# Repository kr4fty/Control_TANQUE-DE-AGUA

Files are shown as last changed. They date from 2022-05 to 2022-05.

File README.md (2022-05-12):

# Control de carga para TANQUE DE AGUA
 La función del circuito es la de encender/apagar un motor el cual llena un<br>
 tanque de agua. Sería reemplazo directo a los conocidos flotadores mecánicos.
<br>

<br>
## Objetivo
 El objetivo es la realización de un circuito que controle al motor, logrando<br>
 el llenado del tanque con la menor cantidad de encendidas. De esta forma se<br>
 intenta ahorrar energía, ya que al encender el motor este consume unas 6 veces<br>
 la corriente nominal de trabajo.<br>
 También se intentara diseñar el circuito con la menor cantidad de componentes y<br>
 de esta forma lograr que sea mas económico en comparación a los flotadores.<br>
 Y por ultimo, el objetivo final seria lograr ser el reemplazo directo, UNO a<br>
 UNO entre los dos dispositivos (electrónico - mecánico), no agregando mas<br>
 cables ni fuentes adicionales a los ya existentes.<br>

## Ventajas
 * Mas económico en comparación al flotador mecánico
 * Menor consumo de energía, ya que solo se activara cuando llegue al nivel<br>
   seteado
 * ...

## Desventajas
 * Fuente de continua, se debería agregar esta fuente para alimentar el control
 * Dependiendo los sensores utilizados, se debería hasta agujerear al taque

## Futuras Modificaciones por mi (Kr4fty)
 * ~~Utilizar una fuente capacitiva que me convierta los 220Vac a los 12Vdc~~
 * ~~Modificar/corregir el circuito, ya que por ejemplo si seteamos que el nivel<br>
   mínimo de agua a un 25% y este sensor falla, es decir queda ABIERTO, el<br>
   motor seguiría funcionando indefinidamente. Lo mismo sucede con el sensor de<br>
   75%~~
 * Optimizar el circuito para tratar de utilizar la menor cantidad de componen_<br>
   tes electrónicos

## Autor original
 [ELECTROALL](https://github.com/ELECTROALL)

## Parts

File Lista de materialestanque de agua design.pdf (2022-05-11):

TANQUE-DE-AGUA

Página 1

Component Count: | 48
Ref | Qnty | Value | Cmp name
BTN1, | | 1 Encendido | SW_DIP_x01
C1, C3, | | 2 470uF | C_Polarized
C2, C4, | | 2 100nF | C
C31, | | 1 1000nF | C
C32, | | 1 100uF | C_Polarized
D1, | | 1 D_Bridge_+-AA | D_Bridge_+-AA
D2, | | 1 20% | LED_Filled
D3, | | 1 40% | LED_Filled
D4, | | 1 60% | LED_Filled
D5, | | 1 80% | LED_Filled
D6, | | 1 100% | LED_Filled
D7, | | 1 ENCENDIDO | LED_Filled
H1, H2, H3, H4, | | 4 MountingHole | MountingHole
J1, | | 1 Vca_IN | Conn_01x02
J2, | | 1 Vca_OUT | Conn_01x02
J5, | | 1 HX30002-BA | Conn_02x03_Odd_Even
Q1, | | 1 2N3904 | 2N3904
R2, R10, R11, R12, R13, R14, | | 6 1K | R_US
R3, | | 1 10K | R_US
R15, R16, R17, R18, R19, | | 5 330R | R_US
R20, R21, | | 2 330R | R_US
R22, | | 1 470R | R_US
R31, | | 1 50R | R_US
R32, | | 1 1M | R_US
SW1, | | 1 Nivel MAX | SW_Push_SPDT
SW2, | | 1 Nivel Min | SW_Push_SPDT
T1, | 1 Transformer_1P_1S Transformer_1P_1S
U1, | | 1 74HC00 | 74HC00
U2, | | 1 ULN2003 | ULN2003
U3, | | 1 LM7805 | LM7805_TO220
U4, | | 1 74HC14 | 74HC14
U5, | | 1 MOC3021M | MOC3021M
U6, | | 1 BTA16-600C | BTA16-600C

TANQUE-DE-AGUA

Página 2

## Footprint

Button_Switch_THT:SW_PUSH_6mm_H4.3mm

Capacitor_THT:CP_Radial_D8.0mm_P3.50mm

Capacitor_THT:C_Disc_D7.5mm_W2.5mm_P5.00mm

Capacitor_THT:C_Rect_L9.0mm_W4.0mm_P7.50mm_MKT

Capacitor_THT:CP_Radial_D8.0mm_P3.50mm

Diode_THT:Diode_Bridge_19.0x3.5x10.0mm_P5.0mm

LED_THT:LED_D3.0mm

LED_THT:LED_D3.0mm

LED_THT:LED_D3.0mm

LED_THT:LED_D3.0mm

LED_THT:LED_D3.0mm

LED_THT:LED_D3.0mm_IRGrey
MountingHole:MountingHole_4.3mm_M4

TerminalBlock_Phoenix:TerminalBlock_Phoenix_PT-1,5-2-5.0-H_1x02_P5.00mm_Horizontal

TerminalBlock_Phoenix:TerminalBlock_Phoenix_PT-1,5-2-5.0-H_1x02_P5.00mm_Horizontal

Connector_PinSocket_2.54mm:PinSocket_2x03_P2.54mm_Vertical

Package_TO_SOT_THT:TO-92_Wide

Resistor_THT:R_Axial_DIN0207_L6.3mm_D2.5mm_P10.16mm_Horizontal

Resistor_THT:R_Axial_DIN0207_L6.3mm_D2.5mm_P10.16mm_Horizontal

Resistor_THT:R_Axial_DIN0309_L9.0mm_D3.2mm_P5.08mm_Vertical

Resistor_THT:R_Axial_DIN0207_L6.3mm_D2.5mm_P10.16mm_Horizontal

Resistor_THT:R_Axial_DIN0207_L6.3mm_D2.5mm_P10.16mm_Horizontal

Resistor_THT:R_Axial_DIN0207_L6.3mm_D2.5mm_P10.16mm_Horizontal

Resistor_THT:R_Axial_DIN0207_L6.3mm_D2.5mm_P10.16mm_Horizontal

Connector_PinHeader_2.54mm:PinHeader_1x03_P2.54mm_Vertical

Connector_PinHeader_2.54mm:PinHeader_1x03_P2.54mm_Vertical

Transformer_THT:Transformer_NF_ETAL_1-1_P1200

Package_DIP:DIP-14_W7.62mm_LongPads

Package_DIP:DIP-16_W7.62mm_LongPads

Package_TO_SOT_THT:TO-220-3_Vertical

Package_DIP:DIP-14_W7.62mm_LongPads

Package_DIP:DIP-6_W7.62mm_LongPads

Package_TO_SOT_THT:TO-220-3_Vertical

TANQUE-DE-AGUA

Página 3

## Description

1x DIP Switch, Single Pole Single Throw (SPST) switch, small symbol

Polarized capacitor

Unpolarized capacitor

Unpolarized capacitor

Polarized capacitor

Diode bridge, +ve/-ve/AC/AC

Light emitting diode, filled shape

Light emitting diode, filled shape

Light emitting diode, filled shape

Light emitting diode, filled shape

Light emitting diode, filled shape

Light emitting diode, filled shape

Mounting Hole without connection

Generic connector, single row, 01x02, script generated (kicad-library-utils/schlib/autogen/connector/)

Generic connector, single row, 01x02, script generated (kicad-library-utils/schlib/autogen/connector/)

Generic connector, double row, 02x03, odd/even pin numbering scheme (row 1 odd numbers, row 2 even numbers), script generated (kicad-library-utils/schlib/autogen/connector/)

0.2A Ic, 40V Vce, Small Signal NPN Transistor, TO-92

Resistor, US symbol

Resistor, US symbol

Resistor, US symbol

Resistor, US symbol

Resistor, US symbol

Resistor, US symbol

Resistor, US symbol

Momentary Switch, single pole double throw

Momentary Switch, single pole double throw

Transformer, single primary, single secondary

quad 2-input NAND gate

High Voltage, High Current Darlington Transistor Arrays, SOIC16/SOIC16W/DIP16/TSSOP16

Positive 1A 35V Linear Regulator, Fixed Output 5V, TO-220

Hex inverter schmitt trigger

Random Phase Opto-Triac, Vdrm 400V, Ift 15mA, DIP6

16A RMS, 600V Off-State Voltage, 35mA Sensitivity, Insulated, Triac, TO-220

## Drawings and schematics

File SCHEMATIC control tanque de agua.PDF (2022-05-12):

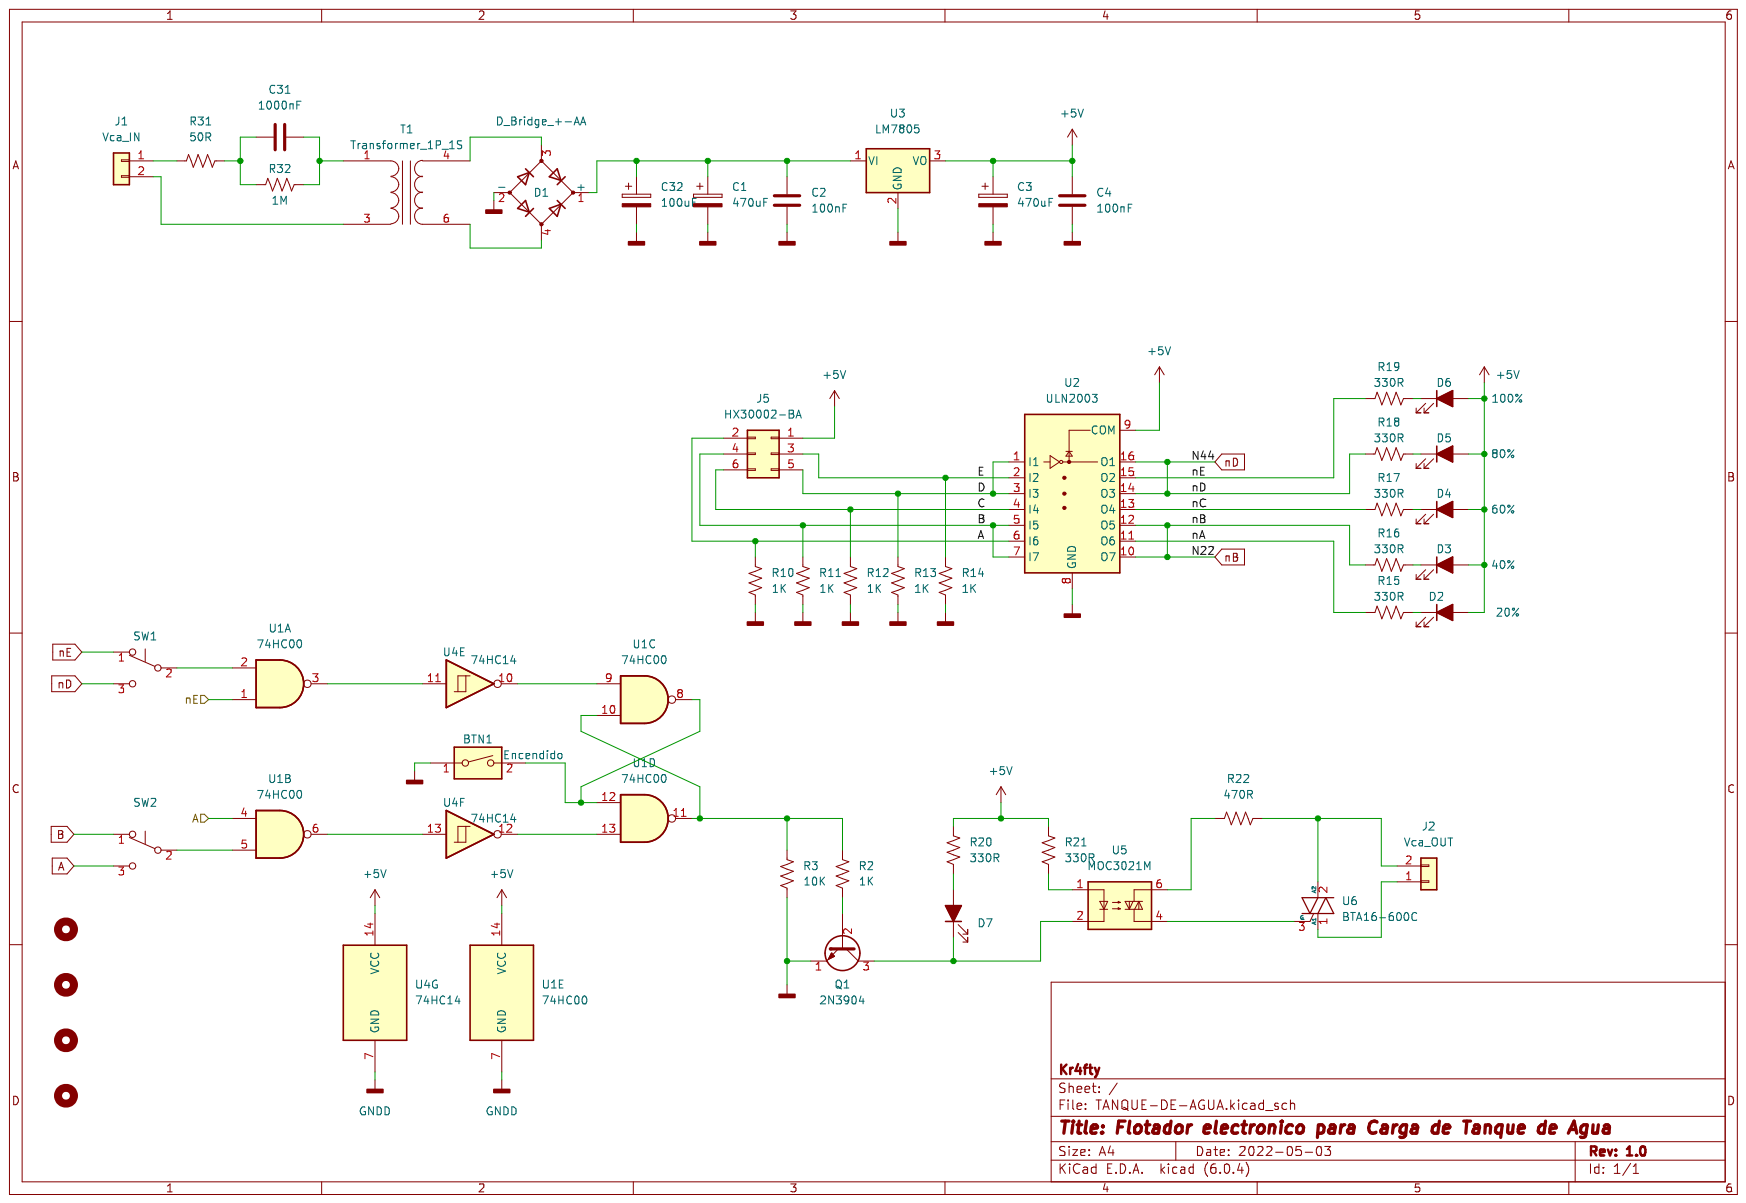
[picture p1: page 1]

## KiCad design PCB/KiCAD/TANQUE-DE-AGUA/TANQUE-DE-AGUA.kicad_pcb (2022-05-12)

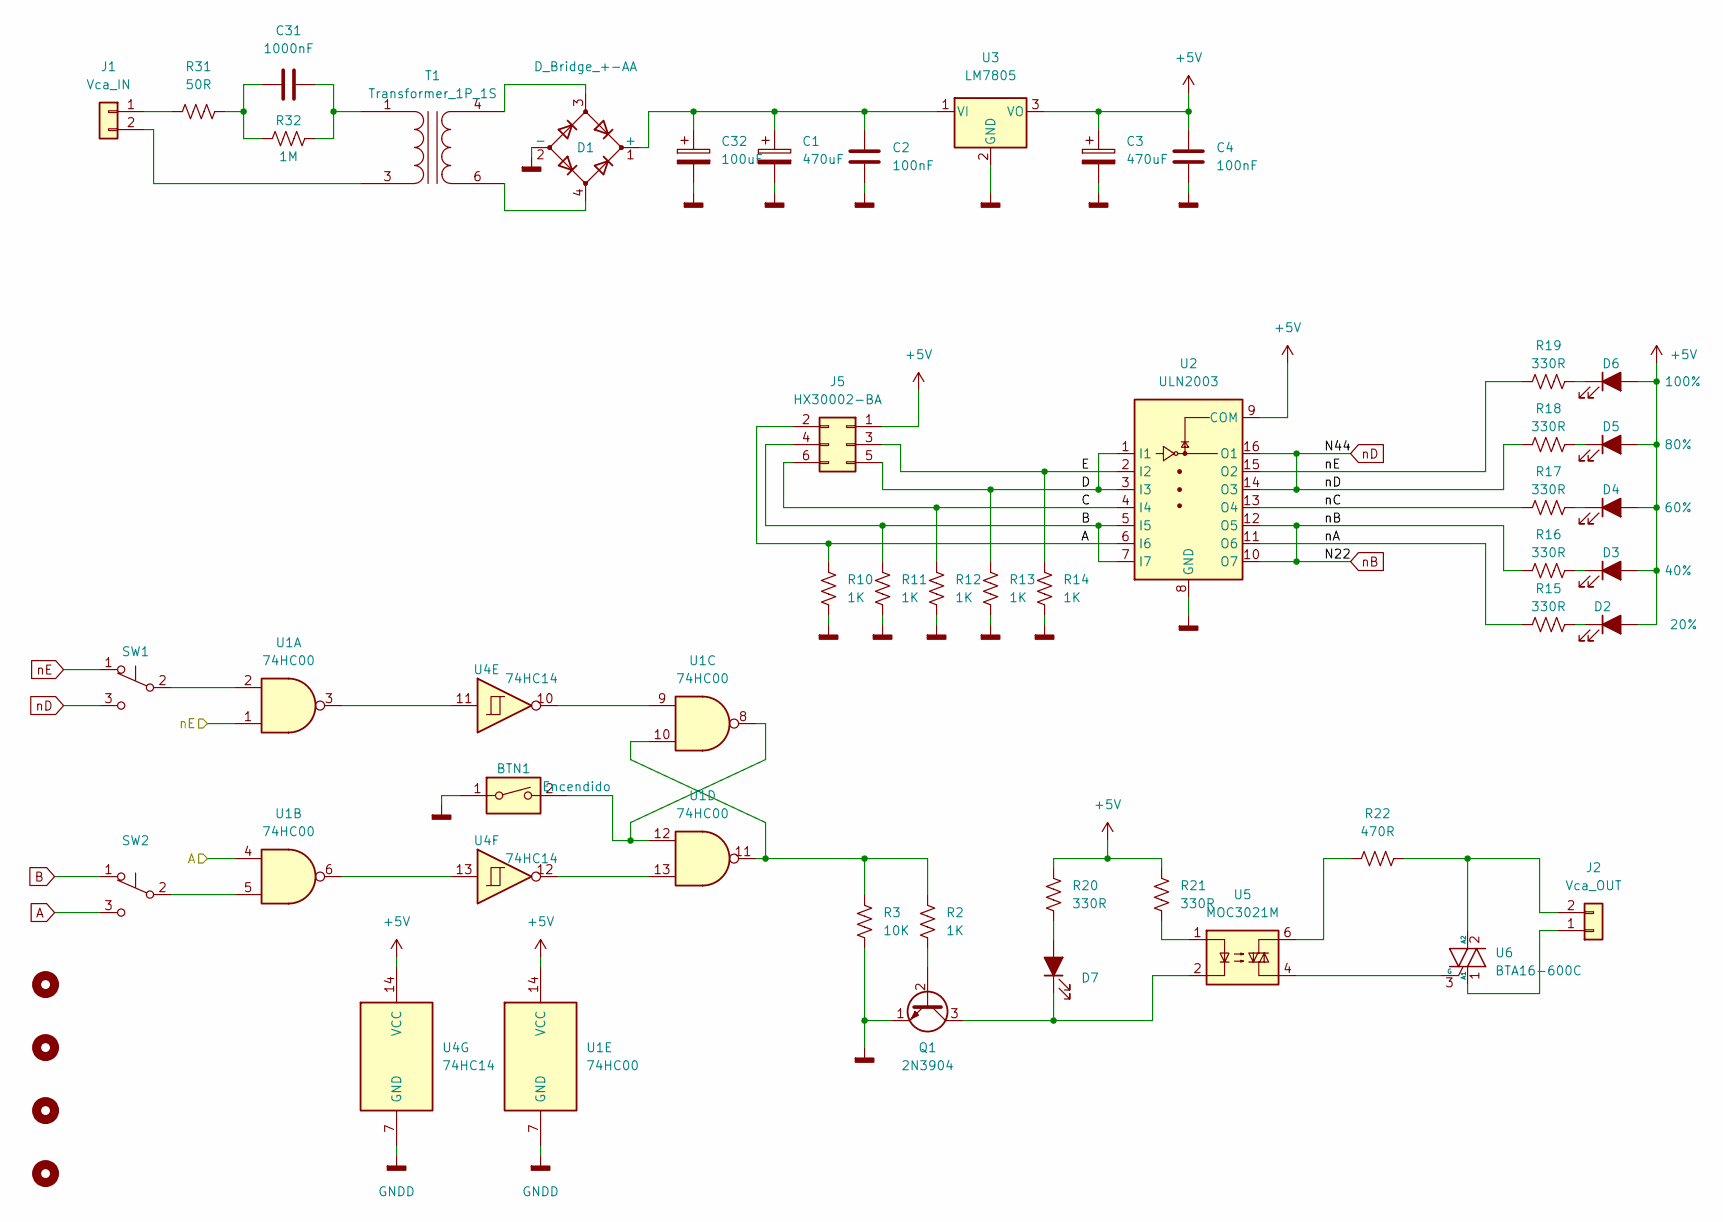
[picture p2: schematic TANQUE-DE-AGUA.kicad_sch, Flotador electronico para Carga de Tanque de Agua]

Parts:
BTN1: Encendido; SW_PUSH_6mm_H4.3mm
C1, C3: 470uF; CP_Radial_D8.0mm_P3.50mm
C2, C4: 100nF; C_Disc_D7.5mm_W2.5mm_P5.00mm
C31: 1000nF; C_Rect_L9.0mm_W4.0mm_P7.50mm_MKT
C32: 100uF; CP_Radial_D8.0mm_P3.50mm
D1: D_Bridge_+-AA; Diode_Bridge_19.0x3.5x10.0mm_P5.0mm
D2: 20%; LED_D3.0mm
D3: 40%; LED_D3.0mm
D4: 60%; LED_D3.0mm
D5: 80%; LED_D3.0mm
D6: 100%; LED_D3.0mm
D7: ENCENDIDO; LED_D3.0mm_IRGrey
H1, H2, H3, H4: MountingHole; MountingHole_4.3mm_M4
J1: Vca_IN; TerminalBlock_Phoenix_PT-1,5-2-5.0-H_1x02_P5.00mm_Horizontal
J2: Vca_OUT; TerminalBlock_Phoenix_PT-1,5-2-5.0-H_1x02_P5.00mm_Horizontal
J5: HX30002-BA; PinSocket_2x03_P2.54mm_Vertical
Q1: 2N3904; TO-92_Wide
R2, R10, R11, R12, R13, R14: 1K; R_Axial_DIN0207_L6.3mm_D2.5mm_P10.16mm_Horizontal
R3: 10K; R_Axial_DIN0207_L6.3mm_D2.5mm_P10.16mm_Horizontal
R15, R16, R17, R18, R19: 330R
R20, R21: 330R; R_Axial_DIN0207_L6.3mm_D2.5mm_P10.16mm_Horizontal
R22: 470R; R_Axial_DIN0207_L6.3mm_D2.5mm_P10.16mm_Horizontal
R31: 50R; R_Axial_DIN0207_L6.3mm_D2.5mm_P10.16mm_Horizontal
R32: 1M; R_Axial_DIN0207_L6.3mm_D2.5mm_P10.16mm_Horizontal
SW1: Nivel MAX; PinHeader_1x03_P2.54mm_Vertical
SW2: Nivel Min; PinHeader_1x03_P2.54mm_Vertical
T1: Transformer_1P_1S; Transformer_NF_ETAL_1-1_P1200
U1: 74HC00; DIP-14_W7.62mm_LongPads
U2: ULN2003; DIP-16_W7.62mm_LongPads
U3: LM7805; TO-220-3_Vertical
U4: 74HC14; DIP-14_W7.62mm_LongPads
U5: MOC3021M; DIP-6_W7.62mm_LongPads
U6: BTA16-600C; TO-220-3_Vertical

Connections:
+5V: C3.1, C4.1, D2.2 (A), D3.2 (A), D4.2 (A), D5.2 (A), D6.2 (A), J5.1, R20.1, R21.1, U1.14 (VCC), U2.9 (COM), U3.3 (VO), U4.14 (VCC)
/C: J5.6, R12.1, U2.4 (I4)
/D: J5.5, R13.1, U2.1 (I1), U2.3 (I3)
/E: J5.3, R14.1, U2.2 (I2)
/nA: R15.1, U2.11 (O6)
/nC: R17.1, U2.13 (O4)
A: J5.2, R10.1, SW2.3 (C), U1.4, U2.6 (I6)
B: J5.4, R11.1, SW2.1 (A), U2.5 (I5), U2.7 (I7)
GNDD: BTN1.1, C1.2, C2.2, C3.2, C4.2, C32.2, D1.2 (-), Q1.1 (E), R3.2, R10.2, R11.2, R12.2, R13.2, R14.2, U1.7 (GND), U2.8 (GND), U3.2 (GND), U4.7 (GND)
unnamed: BTN1.2, U1.8, U1.12
unnamed: C1.1, C2.1, C32.1, D1.1 (+), U3.1 (VI)
unnamed: C31.1, R31.2, R32.1
unnamed: C31.2, R32.2, T1.1 (AA)
unnamed: D1.3, T1.4 (SB)
unnamed: D1.4, T1.6 (SA)
unnamed: D2.1 (K), R15.2
unnamed: D3.1 (K), R16.2
unnamed: D4.1 (K), R17.2
unnamed: D5.1 (K), R18.2
unnamed: D6.1 (K), R19.2
unnamed: D7.1 (K), Q1.3 (C), U5.2
unnamed: D7.2 (A), R20.2
unnamed: J1.1, R31.1
unnamed: J1.2, T1.3 (AB)
unnamed: J2.1, U6.1 (A1)
unnamed: J2.2, R22.1, U6.2 (A2)
unnamed: Q1.2 (B), R2.2
unnamed: R2.1, R3.1, U1.10, U1.11
unnamed: R21.2, U5.1
unnamed: R22.2, U5.6
unnamed: SW1.2 (B), U1.2
unnamed: SW2.2 (B), U1.5
unnamed: U1.3, U4.11
unnamed: U1.6, U4.13
unnamed: U1.9, U4.10
unnamed: U1.13, U4.12
unnamed: U5.4, U6.3 (G)
nB: R16.1, U2.10 (O7), U2.12 (O5)
nD: R18.1, SW1.3 (C), U2.14 (O3), U2.16 (O1)
nE: R19.1, SW1.1 (A), U1.1, U2.15 (O2)

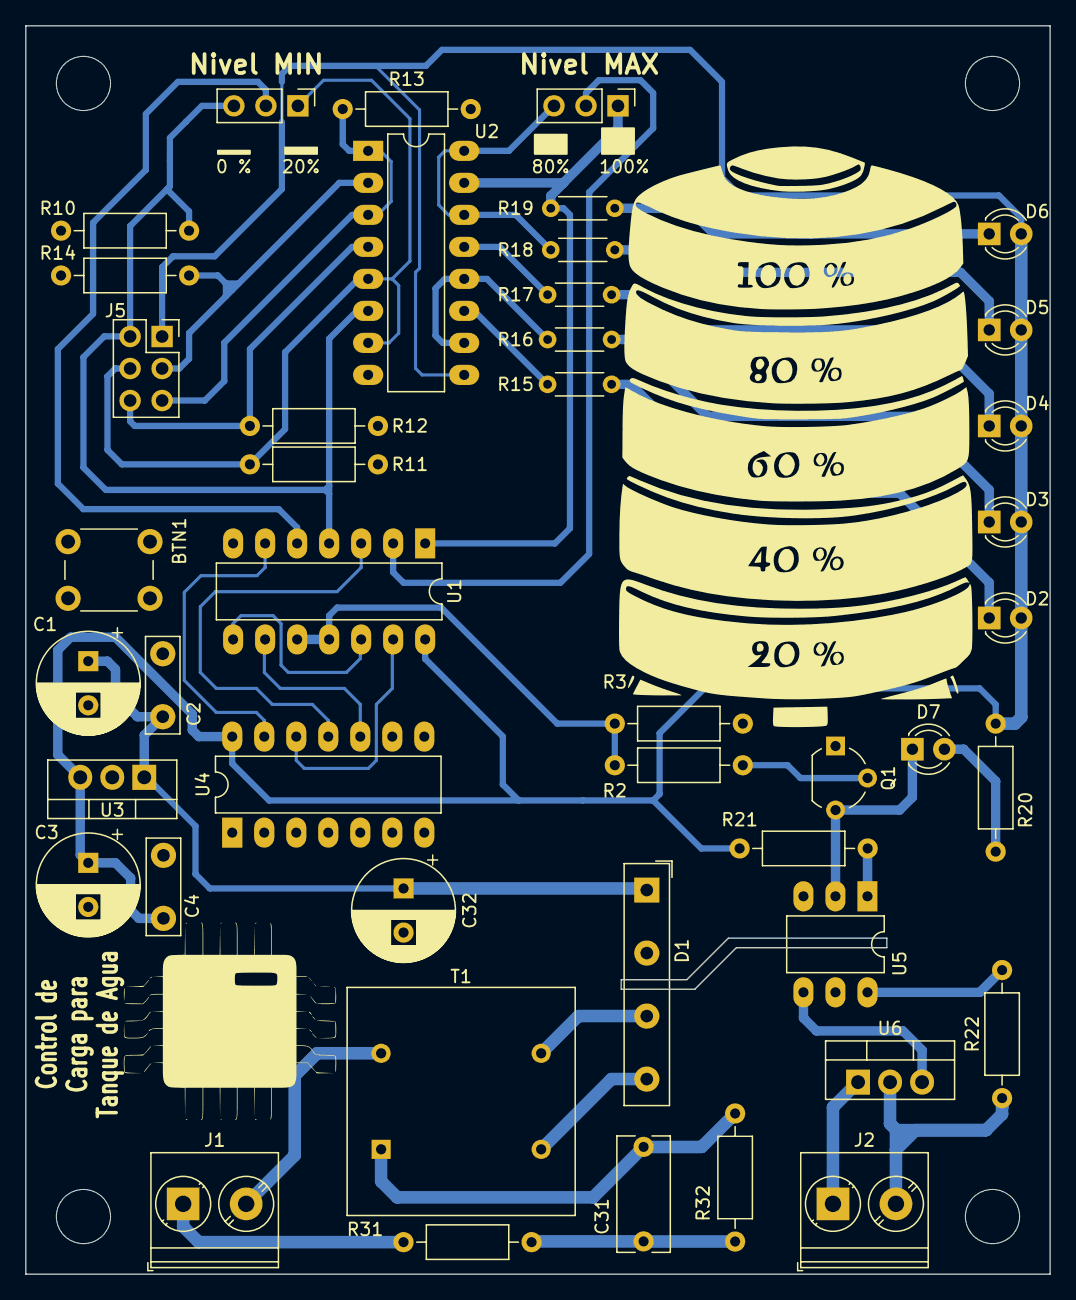
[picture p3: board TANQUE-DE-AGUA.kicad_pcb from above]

Board: 2 copper layers, 81.3 x 99.1 mm, 49 parts (0 on the bottom side), 40 nets.

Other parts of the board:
G1: LOGO; Tanque

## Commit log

2022-05-03 comenzando con mi fork
    [TANQUE-DE-AGUA.kicad_pcb, TANQUE-DE-AGUA.kicad_sch]
2022-05-07 En caso de bloquedo de sensor, forzar apagado
    [TANQUE-DE-AGUA.kicad_sch]
2022-05-09 Actualizacion del diagrama y primer bosquejo del PCB hecho en KiCAD
    [TANQUE-DE-AGUA.kicad_pcb, TANQUE-DE-AGUA.kicad_sch]
2022-05-09 actualizacion del esquematico en Proteus y en KiCAD
    [TANQUE-DE-AGUA.kicad_pcb, TANQUE-DE-AGUA.kicad_sch]
2022-05-09 actualizacion de la lista de materiales
2022-05-10 actualizacion del PCB
    [TANQUE-DE-AGUA.kicad_pcb, TANQUE-DE-AGUA.kicad_sch]
2022-05-10 add board gif
2022-05-11 se agrega Fuente capacitiva
    [TANQUE-DE-AGUA.kicad_pcb, TANQUE-DE-AGUA.kicad_sch]
2022-05-12 update PCB
    [TANQUE-DE-AGUA.kicad_pcb, TANQUE-DE-AGUA.kicad_sch]
